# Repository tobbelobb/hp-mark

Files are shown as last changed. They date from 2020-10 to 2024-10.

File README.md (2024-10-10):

# hp-mark hp-mark logo

Measure Hangprinter externally

Current Hangprinters can only measure their own motor positions.
This is useful, but limited.
hp-mark is a separate solution for measuring a Hangprinter's
positions and orientations of anchors and effector.

# High-Level User-Story Dream
 1. Mount a computer-connected camera
 2. Point camera towards build area
 3. BAM! Hangprinter calibrates itself, and gets ready to start printing with fantastic accuracy & reliability

That user experience might be impossible to achieve, but let's get as close as we can.

# Use Cases by Priority
 0. Establish a coordinate system, with z-axis normal to the build plate
 1. The effector as a measurement device: Measure the effector's position and orientation
 2. Calibrate perfect anchor positions
 3. Measure Hangprinter's positional precision and accuracy
 4. Improve accuracy with static compensation matrix
 5. Detect print disasters
 6. Improve precision by dynamically compensating for measured errors

Comment on use case 2: By combining effector position data with the [auto-calibration-simulation-for-hangprinter](https://gitlab.com/tobben/auto-calibration-simulation-for-hangprinter/-/tree/hp_mark_adjusted), we might find perfect anchor positions without having the anchors in-image.

# History, as of Mar 31, 2021
This project was all about getting good pose estimations, for the first 6 months.
hp-mark was developed as a separate measurement system, with no Hangprinter-specific code or hardware.

We have now started manually executing Hangprinter use cases, like homing and anchor calibration.
See <a href="https://www.youtube.com/watch?v=o8oXp44mtUU">demo 0</a>,
<a href="https://www.youtube.com/watch?v=m9qjuZQowCE">demo 1</a>, and
<a href="https://www.youtube.com/watch?v=yRF-zevGHlQ">demo 2</a>, and
<a href="https://youtu.be/As3Y5J2NTGA">demo 3</a>.

Ahead of us now, is automating it more.

# Status
We can estimate poses with one camera, stably and reliably. [Tweet](https://twitter.com/tobbelobb/status/1377256553665990659).

 - [x] Acquire hardware
 - [x] Calibrate camera
 - [x] Acquire training/benchmark images
 - [x] Calculate one 3D point from one marker
 - [x] Calculate _n_ single points from _n_ markers
 - [x] Calculate 6D pose from 6 points (solve perspective-6-point, or P6P problem)
 - [x] Acquire camera 6D pose (this includes defining our world coordinate system)
 - [x] Acquire effector 6D pose
 - [x] Detect all markers on 95% of training images
 - [x] Create a continuous stream of position measurements (video?)
 - [x] Get a statistical idea about size of error at the origin
 - [ ] Respond to RepRapFirmware/Duet request for position measurement

A checked box above means "good enough for now".

Nice-to-haves:

 - [ ] Take image ourselves upon request, don't rely on other programs to take image first
 - [ ] Get a statistical idea about size of precision and accuracy in the whole measurement volume
 - [ ] Integrate a second camera, to reduce error

# Equipment
 - Raspberry Pi 4 (mine is Model B, 2GB RAM)
 - Arducam 8 MP Sony IMX219 camera module
 - Lens: M2504ZH05 Arducam lens
 - 32GB U3 SD card
 - Default recommended Raspberry Pi OS, 32-bit
 - OpenCV 4.4.0
 - EDLib for ellipse detection
 - Probably a separate computer ("desktop" or "laptop" or "main computer") for running hpm. You can run hpm directly on the Raspberry Pi, but it's slow.

# How To Clone/Pull This Repository

 - Clone with `git clone --recursive https://gitlab.com/tobben/hp-mark.git`. The `--recursive` is there to make sure you get the `hpm` submodule.
 - If you already did `git clone` without `--recursive`, do `git submodule init && git submodule update` to get submodule code right.
 - When you pull the hp-mark repo, since the `hpm` submodule might also have changed since last time, do either one of
   ```
   git pull; cd hpm; git pull; cd ..
   ```
   or
   ```
   git pull --recurse-submodules
   ```

# How To Use This Repository

First calibrate your camera.
How to do that is described in [the README.md in camera-calibration directory](./camera-calibration/README.md).

Then compile `hpm`.

# hpm
hpm is the core part of hp-mark.
It is a program that reads data from the camera, and outputs a pose (three rotational values, three translational values).

## hpm Dependencies
This repo will (for now) assume that a number of dependencies are already installed by the user.

#### Main Computer
 - OpenCV 4.2.0 or later
 - g++ version 10 or later
 - build2 version 0.13.0 or later (not required if you're only going to build once)
 - clang++ version 10 or later (not required for build & use)
 - clang-tidy version 10 or later (not required for build & use)
 - clang-format version 10 or later (not required for build & use)
 - compiledb (not required for build & use)
 - shfmt (not required for build & use)
 - python3 (not required for build & use)
 - black (not required for build & use)
 - scipy (not required for build & use)
 - numpy (not required for build & use)

#### Raspberry Pi 4
 - rpicam-still (shading fix required if you don't use standard Raspberry Pi Picam. For why, and how to get the right shading fixes for Arducam lenses see [here](https://www.arducam.com/docs/cameras-for-raspberry-pi/native-raspberry-pi-cameras/lens-shading-calibration/).)

### Why Are Some Dependencies Not Required for hpm Build & Use?
Scripts `tidy.sh`, `make-compilation-database.sh`, `format.sh` etc are there to softly enforce some coding quality and standards.
It you're not going to change the code anyways, then you don't need the scripts nor their dependencies.

### Why Is build2 Not Required Always?
build2 is a fast build system, but it takes a while to get it.
If you only need to build once, you can build without any build system, and use the script `hpm/hpm/slow_build.sh` instead.

It will be a very slow build, but it will take less time than it would have taken
to acquire build2.

## hpm How To Build
First, you need a fairly recent version of OpenCV installed somewhere in your C++ compilers' search path.
You can probably use your system's package manager. On Ubuntu, something like
```
sudo apt install libopencv-dev
```

If you're on another system, see OpenCV's or your operating system's official build/install instructions.

Back in the day, I had to build OpenCV myself.
See <href="./doc/simplest-hpm-compilation-ubuntu-20.04">simplest-hpm-compilation-ubuntu-20.04</a> if you for some reason need to do that.

### For Users Who Only Build Once
```
sudo apt install libopencv-dev
cd hp-mark/hpm/hpm
./slow_build.sh --no-tests
```

Then try running the resulting `hpm` binary:
```
./hpm --help
```

I'm not using it directly most of the time.
Rather, I'm using it via the scripts found in
the hp-mark/use directory

### For An Advanced User Who Wants To Build Repeatedly
Build with build2. See <a href="https://build2.org">build2.org</a> for install instructions.

Before building `hpm` with build2, its recommended to create a build configuration.
No pre-configured build configuration is shipped with this project, and build2's default configuration works poorly with hpm.

```
cd <path-to>/hp-mark/hpm
bdep init --config-create ../my-build-dir @user cc config.cxx=g++-10
```
This creates a build2 config, gives it the location `../my-build-dir`, the name `@user`, and the compiler `g++-10`.
Compile with
```
b
```

### If You're a Developer Making a Pull Request
Create a configuration with some more compiler flags than the user:
```
cd <path-to>/hp-mark/hpm
#in < path - to > / hp - mark / hpm
bdep init --config-create ../my-advanced-config @developer cc config.cxx=g++-10 config.cxx.coptions="-g -Wall -Wextra -Wold-style-cast -Wnon-virtual-dtor -pedantic -Wcast-align -Wunused -Woverloaded-virtual -Wpedantic -Wconversion -Wsign-conversion -Wmisleading-indentation -Wnull-dereference -Wdouble-promotion -Werror -O2 -march=native"
```
You can edit your personal or compiler specific flags later, in `<path-to>/hp-mark/my-advanced-config/build/config.build`.
Some example flags for reference can be seen in `<path-to>/hp-mark/hpm-gcc/build/config.build`.

Compile with
```
b test
```
which will build and test using your default build config.

Symlinks to executables end up in `<path-to>/hp-mark/hpm/hpm/`.
The executables themselves, as well as build artifacts, end up in `../my-build-dir/hpm/hpm/` or `../my-advanced-config/hpm/hpm/`, depending on which build you updated.

Create as many configs as you want.
One that cross compiles for the Raspberry Pi 4 might be particularly useful in the later stages of this project, when build times get noticeable.

You can see all your configs, and which of them is the default with
```
bdep config list
```
bdep is a very flexible and useful command. See its documentation [here](https://build2.org/bdep/doc/bdep-config.xhtml).

I use [some own notes](https://gitlab.com/hangprinter/linc/-/blob/master/README.md) for remembering build2 commands.

## How To Run
Your executable should tell you how it wants to be used.
Ask it like this:
```
<path-to>/hp-mark/hpm/hpm/hpm
```
or, like this:
```
cd <path-to>/hp-mark/hpm/hpm/
./hpm
```

The executable will tell you that it wants some camera parameters (a config file).
Examples of camera parameter configs are given in `hp-mark/hpm/hpm/example-cam-params/`.
They contain the outputs of your camera calibration, as well as `camera-rotation` and
`camera-translation` that are created by `hpm` itself, if it's executed with the `-c/--camera-position-calibration` flag.

To get the correct `camera-rotation` and `camera-translation`:

 1. Place your effector at home position (nozzle in origin, lines tight, effector horizontal).
 2. Mount your camera in it's final position, pointing towards the effector.
 3. Take the image (and maybe download to your main computer, if that's where you execute `hpm`).
 4. Run `$ ./hpm <your-half-finished-camera-parameters-file> <marker-parameters> <image-file> --camera-calibration`

### But Wait, We Don't Have The Correct Marker Parameters Yet!
True. Marker parameters is another config file, that describes your markers.
Examples of such configs are found in `hp-mark/hpm/hpm/example-marker-params/`.
They contain:

 * Maker positions on the effector
 * Marker type on the effector
 * Marker size on the effector
 * Optionally: marker positions on the bed
 * Optionally: marker type on the bed
 * Optionally: marker size on the bed

Your marker type is most probably disk, but hpm also supports sphere.
Your marker diameter is 90 mm if you follow my standard example. Bigger is generally better.
Your marker positions are a bit more complicated.
We want their xyz positions relative to the tip of the nozzle, in a coordinate system that looks like this:

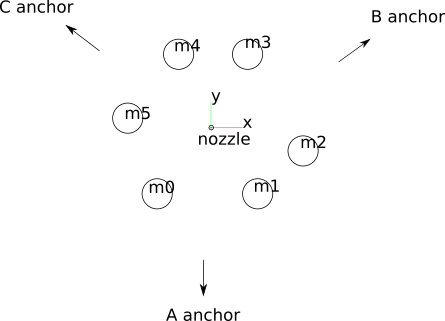
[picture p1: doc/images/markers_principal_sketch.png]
markers principal sketch


It's very hard to take these xyz measurements directly.

You have two options for how to get these xyz measurements.

#### Option 1: Try Markers Positions Detector

Getting the xyz measurements of the markers can be done with computer vision. Dzardajs (aka Github user matusbalazi) has made [Markers Positions Detector](https://github.com/matusbalazi/markers_positions_detector) to help you do that. At the time of writing (April 8, 2022) Markers Positions Detector is still quite new, but I recommend that you try this out first if you already have a well-calibrated camera.

#### Option 2: The find-marker-positions.py Script

This is the old way, like a precursor to Markers Positions Detector.

If you want to use find-marker-positions.py, there will be 21 manual measurements.
They are all either between the center of a marker to the tip of the nozzle,
or between two centers of markers.
Referring to the image, Make the following measurements in the following order:

 * nozzle-m0, nozzle-m1, nozzle-m2, nozzle-m3, nozzle-m4, nozzle-m5
 * m0-m1, m0-m2, m0-m3, m0-m4, m0-m5,
 * m1-m2, m1-m3, m1-m4, m1-m5,
 * m2-m3, m2-m4, m2-m5,
 * m3-m4, m3-m5,
 * m4-m5.

Armed with these 21 values (in units of millimeters), do
```
cd hp-mark/find-marker-positions
./find-marker-positions.py --measurements <all measurements here in correct order, separated by spaces>
```
Alternatively, you can type in your 21 values into the `find-marker-positions.py` script directly. It's near the bottom of the file.
I you do type in directly into the file, you can execute the script with no arguments:
```
./find-marker-positions.py
```

If you get a cost below ca 3, you're probably good.
Copy/paste the final values you get into your marker-params config file.

Congrats! You should now be able to measure the position of your effector with hp-mark.
Take a few test images and see if it works.

#### Usage Via SSH

After a while, it gets cumbersome to always have to download the image from the Raspberry Pi to the main computer manually,
so I've written some scripts to speed that up.

Look into:

```
<path-to>/hp-mark/use/use_ssh_continuous.sh
```

Open it, change `CAMPARAMS` and `MARKERPARAMS` variables so they point to your two new config files.
It accepts the same flags as `hpm` does, so take it for a ride for example like
```
./use_ssh_continuous.sh --show result
```
... and press Enter to get another image, or ctrl-C to exit.

### How to get external camera parameters?
After the correct camera calibration you obtained internal camera parameters stored in the `myCamParams.xml` file.
Then you found markers positions on the effector which are also stored in the XML file.
Last thing we have to do to use hp-mark is to find out external camera parameters (rotation and translation of camera).

I made simple script which will make it easier and faster for you.
It runs hpm, analyzes input image, generates XML file with external camera parameters and merges
internal and external cam params into one XML file.

All you need is:
 * XML file with internal camera parameters
 * XML file with markers parameters
 * image of your effector with markers placed on it

Now install colorama package by typing to command line:

```
sudo apt update
sudo pip install colorama
```

Then run:

```
python3 <path-to>/hp-mark/hpm/hpm/get_cam_params.py
```

There is a bunch of arguments you can add to speed up later process:
 1. `-f1` or `--xmlC` means path to the internal cam params XML file
 2. `-f2` or `--xmlM` means path to the markers params XML file
 3. `-f3` or `--image` means path to the input image which will be analyzed

So the command to run this program can look like this:

```
python3 <path-to>/hp-mark/hpm/hpm/get_cam_params.py --xmlC <path-to>/myCamParams.xml --xmlM <path-to>/myMarkersParams.xml --image <path-to>/image.jpg

```

After that `myCamParams.xml` should be generated in the same folder as `get_cam_params.py` is.
Last thing you have to change is `CAMPARAMS` variable in `use_ssh_continuous.sh` file so it points to your new config file.

Another important script, which also tries to move the Hangprinter's effector around between images is called
`get_auto_calibration_data_automatically.sh`.
I won't get into detail about that here. Some detail is offered in the hangprinter.org docs.

# Remaining Development Challenges
 - The cameras' positions are estimated from images of known patterns. The results' accuracy are limited by errors in the markers and errors in the camera calibration values
 - We must calibrate the camera lens to compensate for optical distortion. This is time consuming and hard. The lo-distortion lens from Arducam helps a bit, but not all
   the way.

# Opportunities & Smaller Use Cases
 - There's an interesting PnP solver on its way into OpenCV that seems very good: [Added SQPnP algorithm to SolvePnP (2020)](https://github.com/opencv/opencv/pull/18371)
 - Distances between nozzle and markers may be measured by placing the nozzle on a marker, and letting hp-mark measure relative distances.
 - We can add features in the future that control the image processor (to compensate distortion predictably, or for other tasks). An image processor can do [lots of things](https://webpages.uncc.edu/jfan/isp.pdf). The Raspberry pi 4 and libcamera gives us the perfect tools for the job:
   * [raspberrypi.org page about libcamera](https://www.raspberrypi.org/documentation/linux/software/libcamera/)
   * [libcamera's own home page](http://www.libcamera.org/)
   * [Blog post announcing libcamera](https://www.raspberrypi.org/blog/an-open-source-camera-stack-for-raspberry-pi-using-libcamera/)

# Keywords
 camera localization, pose estimation, motion tracking, optical sensors, vision-based registration, marker-based tracking techniques, fiducial marker localization

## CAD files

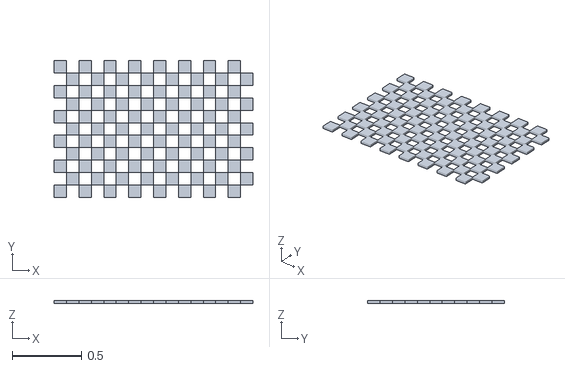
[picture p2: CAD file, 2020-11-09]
camera-calibration/calibrate_openscad_camera/chessmesh.stl
1.44 x 0.99 x 0.02

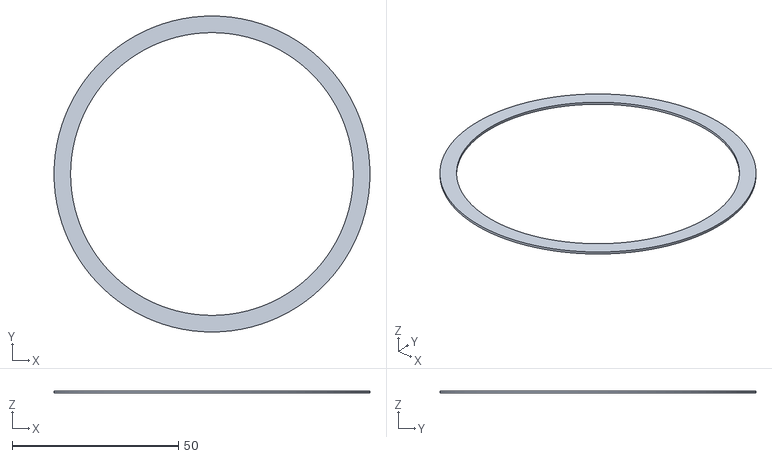
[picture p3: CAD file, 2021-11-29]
markers/flat_markers/contrast_edge.stl
95.0 x 95.0 x 0.7

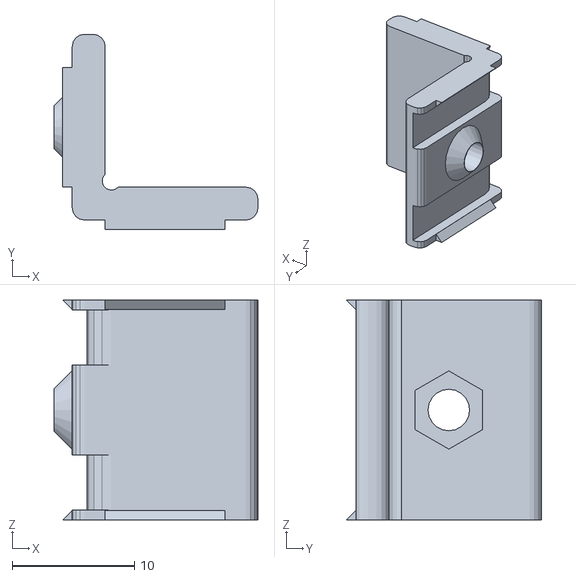
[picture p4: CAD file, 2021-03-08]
markers/marker_slider.stl
16.7 x 16.0 x 18.0

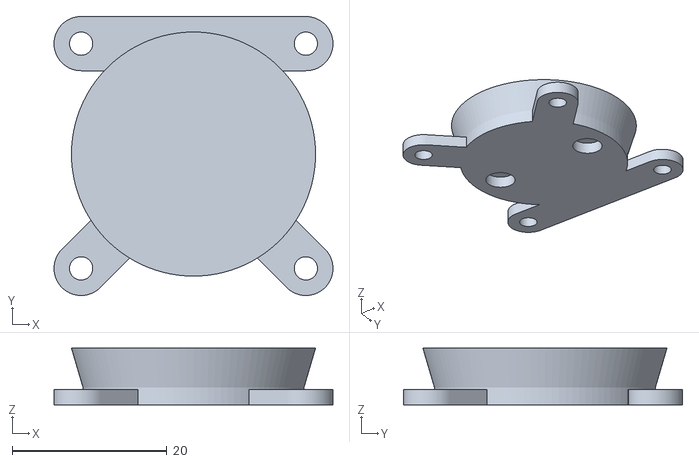
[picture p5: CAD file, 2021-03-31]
picam-mount/snrreskive2_arducam.stl
36.0 x 36.0 x 7.30

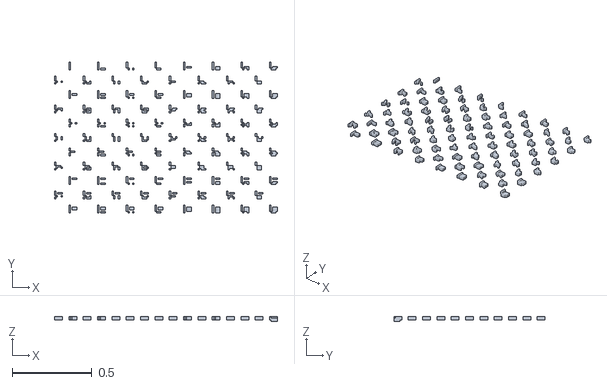
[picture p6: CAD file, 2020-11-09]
camera-calibration/calibrate_openscad_camera/charucointernal.stl
1.40 x 0.95 x 0.03

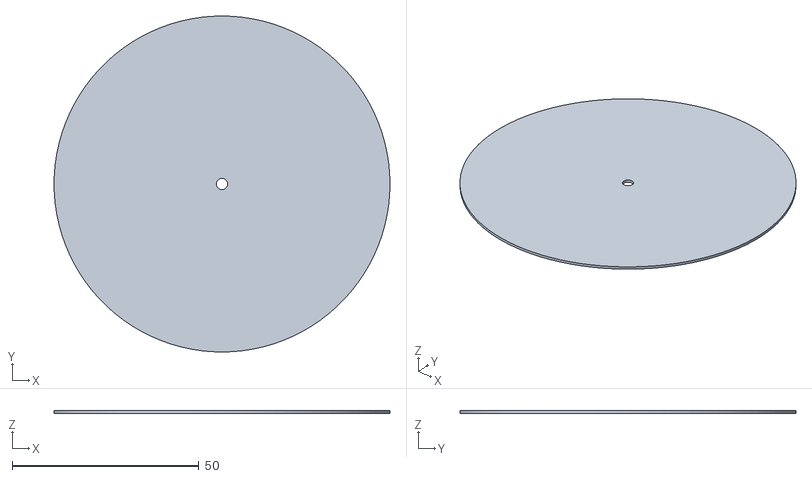
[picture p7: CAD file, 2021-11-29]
markers/flat_markers/retroreflective_plate.stl
90.0 x 90.0 x 0.7

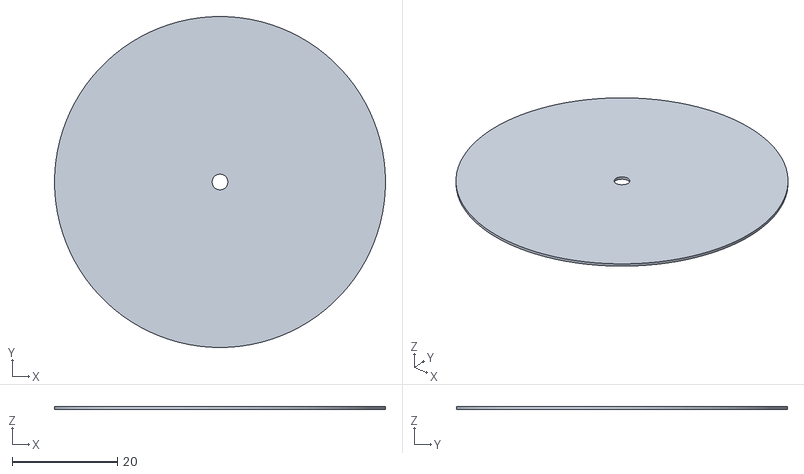
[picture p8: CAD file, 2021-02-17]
markers/spherical_markers/bg_plate.stl
63.0 x 63.0 x 0.5

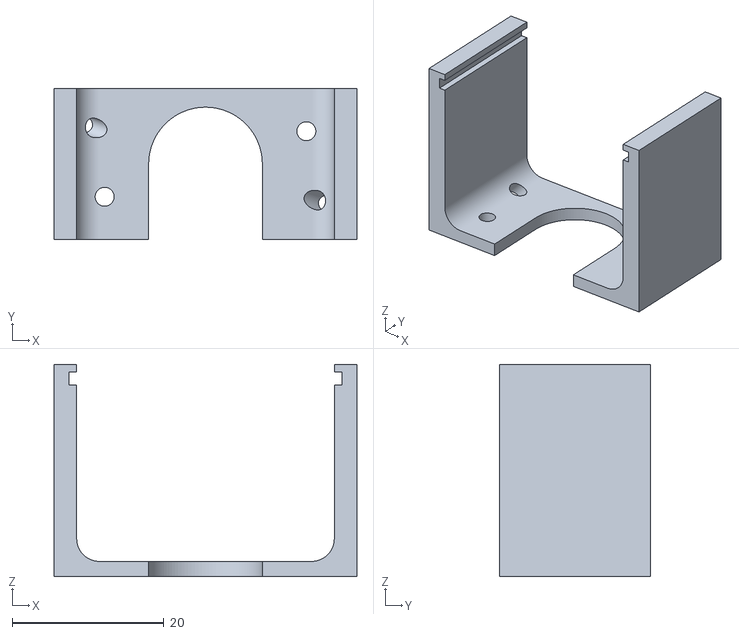
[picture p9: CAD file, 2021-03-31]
picam-mount/led_holder_arducam.stl
40.0 x 20.0 x 28.0

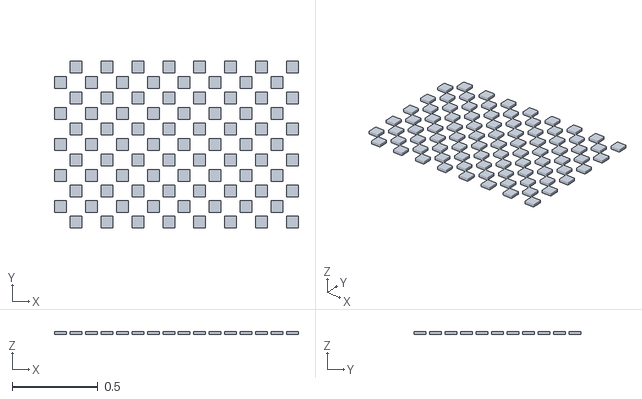
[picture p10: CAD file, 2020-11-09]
camera-calibration/calibrate_openscad_camera/charucomesh.stl
1.42 x 0.97 x 0.02

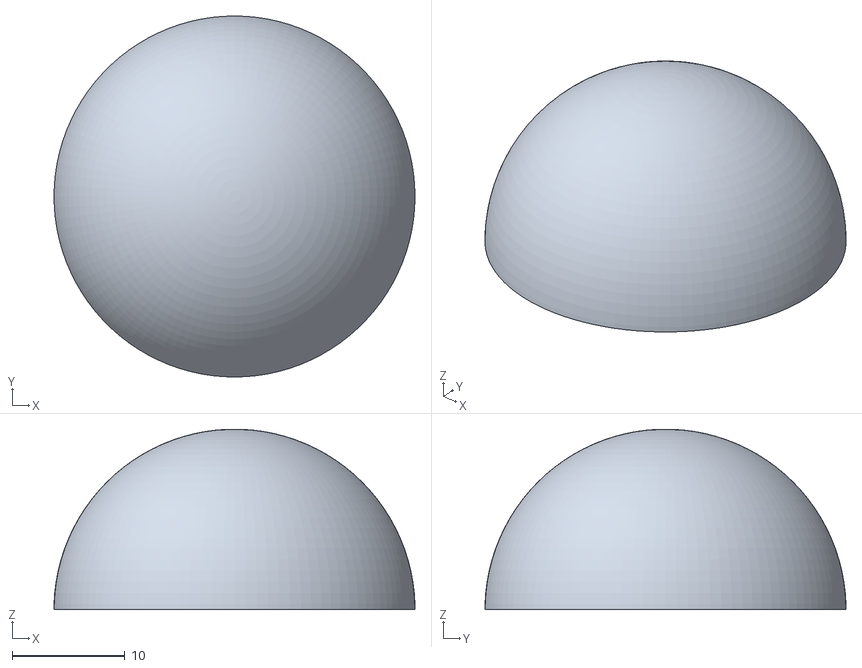
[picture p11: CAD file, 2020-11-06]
markers/spherical_markers/top_cap.stl
32.0 x 32.0 x 16.0

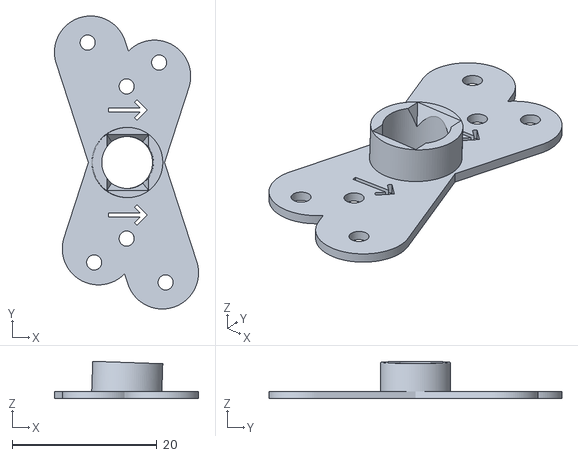
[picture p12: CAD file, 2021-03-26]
picam-mount/lens_hood.stl
19.9 x 40.4 x 5.17

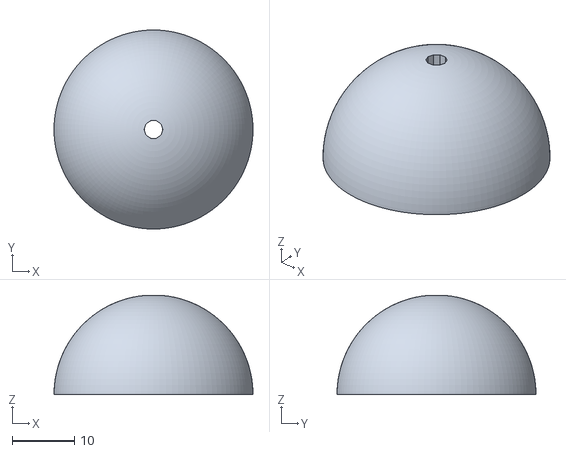
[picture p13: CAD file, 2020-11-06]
markers/spherical_markers/bottom_cap.stl
32.0 x 32.0 x 15.9

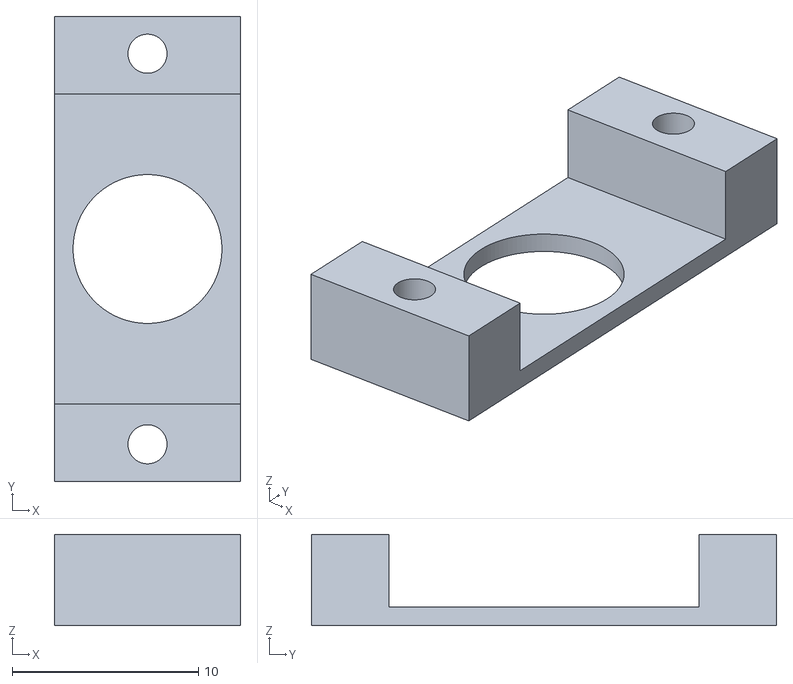
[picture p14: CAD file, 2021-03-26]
picam-mount/lens_hood_legs.stl
10.0 x 25.0 x 4.90

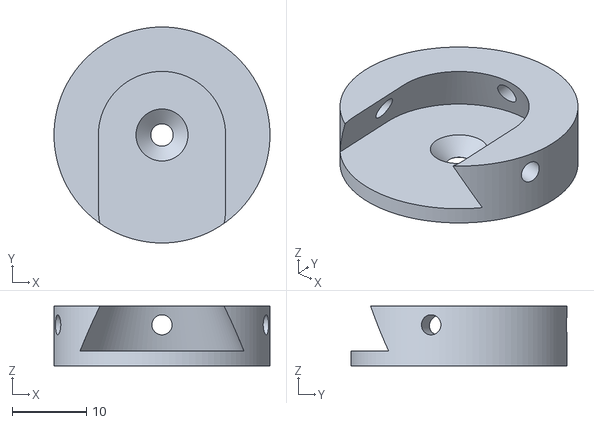
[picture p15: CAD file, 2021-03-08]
picam-mount/base.stl
29.0 x 29.0 x 8.00

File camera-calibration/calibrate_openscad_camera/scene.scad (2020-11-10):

// For some reason, we've lost perfect squareness by ~.1%
// It might be the pdf that is off, or it might be the program
// pdf2svg that has bad truncation errors internally,
// or it might be Blender that has the truncation errors.
// Blender was used to convert the intermediate svg image into
// chessmesh.stl, charucomesh.stl, and charucointernal.stl
measured_x_length = 1440.0297403;
measured_y_length = 989.8103476;

// With these lengths, each chess square side is 90 mm wide
// And each marker is 70 mm wide
wanted_x_length = 1440;
wanted_y_length = 990;

translate([-wanted_x_length/2, wanted_y_length/2, 0]) {
  scale([wanted_x_length/measured_x_length, wanted_y_length/measured_y_length,1]) {
    color("black")
      scale([1000, 1000, 0.005])
      import("./chessmesh.stl");
    color("black")
      scale([1000,1000,0.005])
      import("./charucomesh.stl");
    color("white")
      translate([0,0,-0.0005])
      scale([1000,1000,0.25])
      import("./charucointernal.stl");
  }
}
//$t=0.7;

// Ok, but not fantastic values
//$vpr = [45,0,360*$t];
//$vpt = [130*sin(360*$t),-130*cos(360*$t),0];
//$vpd = 2500+1000*abs(sin(360*2*$t));

// For animating a bunch of frames, you can use this
vprs = [[ 49.90, 0.00, 359.60 ],
        [ 52.70, 0.00, 29.00 ],
        [ 53.40, 0.00, 60.50 ],
        [ 46.40, 0.00, 90.60 ],
        [ 47.80, 0.00, 120.70 ],
        [ 42.90, 0.00, 154.30 ],
        [ 34.50, 0.00, 180.20 ],
        [ 50.60, 0.00, 196.30 ],
        [ 52.00, 0.00, 221.50 ],
        [ 48.50, 0.00, 261.40 ],
        [ 49.20, 0.00, 279.60 ],
        [ 51.30, 0.00, 323.70 ]];
vpts = [[ -2.39, -66.23, 37.04 ],
        [ 37.14, -122.39, -54.19 ],
        [ 136.35, 12.34, -81.12 ],
        [ 107.45, 12.39, -49.25 ],
        [ 91.81, 65.31, -63.52 ],
        [ 80.53, 52.77, -48.47 ],
        [ -7.27, 54.79, -48.38 ],
        [ 50.34, 79.79, -78.75 ],
        [ -94.89, -6.90, -120.59 ],
        [ -75.61, -43.08, -92.93 ],
        [ -73.70, -38.31, -89.82 ],
        [ -90.66, -35.63, -99.43 ]];
vpds = [2264.24, 2296, 2557, 2547.78, 2886, 2800, 2215, 2215, 2673, 2673, 2673, 2592];

// Writing a bash script with OpenScad echo function...
//for (i=[0:len(vprs)-1]) {
//  echo(vpts[i], vprs[i], vpds[i]);
//}

//index = round($t*len(vprs));
//$vpr = vprs[index];
//$vpt = vpts[index];
//$vpd = vpds[index];

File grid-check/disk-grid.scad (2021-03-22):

// Use command line to create renders.
// For example

// openscad --camera 0,0,0,0,0,0,2000 --imgsize 15360,8058 --colorscheme Nature --projection perspective -o grid-blue-2000.png sphere-grid.scad


$fn=2000;

squareWidth = 100;
gridWidthx = 7;
gridWidthy = 4;
//$vpt=[0,0,0];
//$vpr=[0,0,0];
//$vpd=2000;

for (nx = [-gridWidthx:gridWidthx])
  for (ny = [-gridWidthy:gridWidthy])
    translate([nx*squareWidth, ny*squareWidth, 0])
      color([1,1,1])
        cylinder(d=70, h=0.01);

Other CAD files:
picam-mount/vippeplate.stl
picam-mount/snurreskive.stl
picam-mount/snurreskive2.stl
markers/spherical_markers/screw.stl
grid-check/sphere-grid.scad
grid-check/tilted-disk-grid.scad
camera-calibration/calibrate_openscad_camera/test.scad
markers/marker.scad
markers/revolve2.scad
picam-mount/picam_mount.scad

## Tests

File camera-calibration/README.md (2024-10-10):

# How To Calibrate PiCam v2 for hp-mark

We're going to use a [charuco board](https://docs.opencv.org/4.4.0/da/d13/tutorial_aruco_calibration.html)
as our pattern.

We're also going to use [a non-linear optimization method](https://elib.dlr.de/71888/1/strobl_2011iccv.pdf)
to compensate for the paper with the charuco board on being every so slightly non-flat.

## Preparations

Read this whole document first.
You might want to do things in a different order than described here,
so read the whole document first to avoid time consuming surprises later.
You can always come back here and follow step-by-step later.

Print the charuco board pdf as large as you can.
Tape/glue your charuco board down as flat and straight as possible.

Compile and take the camera calibration program for a test run:
(Warning: this takes a few minutes to run on the Raspberry pi 4.)
```
cd <path-to>/hp-mark/camera-calibration
./doit.sh
```

If everything went smooth, an output file `myCamParams.xml` should have been created.
It contains nonsense, but we hopefully confirmed that the compiler and the program itself are working.

Next remove it and the test images.
(Take a look at them first, they should be decent examples.)

```
rm myCamParams.xml pics/camera*
```

## How To Take Calibration Images

The duet3 official Raspberry Pi OS image comes with the camera disabled by default.
To enable it do
```
sudo raspi-config
[Interface Options] -> [Camera] -> [Enable] -> [Reboot yes]
```

Take your own pics inside the pics directory.
```
cd pics
./takeCalibrationStills.sh
```

Press Enter to take a picture, press X followed by enter before the last image.

Regardless if your first pics are good or bad, put their names in the `pics_list.xml`, and
execute `doit.sh` like before.
You will probably get an error the first time, because all the corners could not be identified in
some, or all of your image(s).

Look into the script `takeCalibrationStills.sh` and adjust each of the flags to `rpicam-still`
until you get nice image quality.

Take note of the `-fs/--framestart` flag.
Increment the framestart if you want to avoid overwriting previously taken images.

We want to not have over-exposure, as it would affect calibration negatively.
Reduce the `--shutter` time until the white squares look light grey on your image.

Also, adjust the focus of your Picam v2.
Optimize for the distance range of the final use case, not for the calibration itself.
If you later change the focus, you will need to re-calibrate the camera.

## How To Take Good Calibration Images

Read [Dr. Strobl's invaluable calibration hints](https://www.dlr.de/rm/en/desktopdefault.aspx/tabid-3925/6084_read-9196/).
Here's a procedure that tries to take the advice into account as much as we can in our use case:

  * Fasten your Picam to a camera tripod or similar, at 25-27 cm height
  * Move the camera around the pattern and take images
  * Fill as large portion of the image with squares as you can
  * All aruco markers must be in every image
  * Don't touch or move the pattern between images
  * Take half of the images with the camera mounted upside down (otherwise we risk getting better calibration in the upper half of the image, where focus is sharper)

Here's an image of my "imaging lab" during calibration image grab.

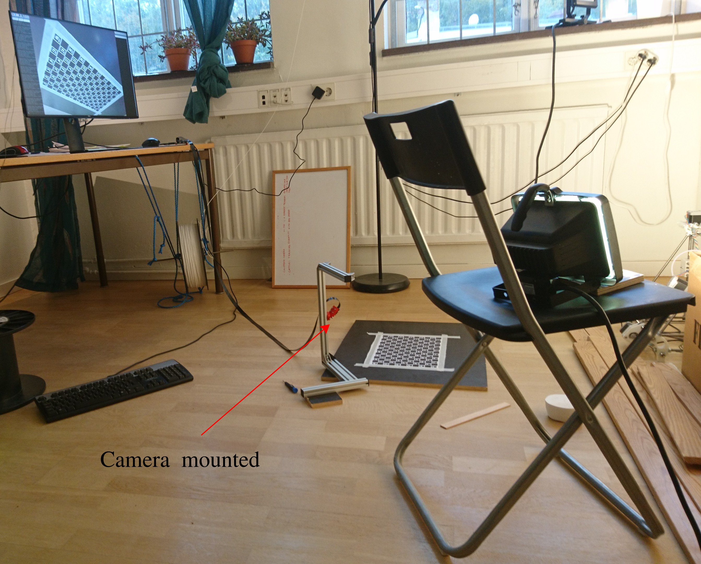
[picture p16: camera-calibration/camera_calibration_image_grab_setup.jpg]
camera calibration image grab setup


If you have a large flatish screen, you may just display the pattern on that screen, instead of printing it on paper:

camera calibration pattern shown on screen.

## How To Use the Calibration Images Well

Run `./doit.sh` to double check that all corners of all images in `pics_list.xml` are detected.
You might get better detection my incrementing/decrementing `adaptiveThreshWinSizeStep` inside `detector_params.yml` by 1 or 2.
There's [a whole tutorial](https://docs.opencv.org/4.4.0/d5/dae/tutorial_aruco_detection.html) about Aruco detection in the OpenCV documentation.

Once you have 10-20 good images with full corner detection in your `pics_list.xml`, it's time to do some final tuning.

Measure the square side length of your charuco board as accuratly as you can.
If your paper is even slightly wrinkled, remember that each square will appear shortened by that if you measure across several squares at once.
We don't want to include the losses from paper wrinkling in our measurement, we want the real width of a stretched square.
Also, squares will have different widths on different portions of your paper (unless your printer is really high-end),
so measure several times on different parts of the paper, and use the average of your measured values.

In a similar fashion, measure the side lengths of the aruco markers.
Getting the aruco size really accurate is less important than getting the square size right.
Focus your effort on the square size.

Open `doit.sh` and feed in your measured `--square_side_length` and `--marker_side_length`.
It doesn't matter which units you use.

The last value we need is the `--grid_width`:

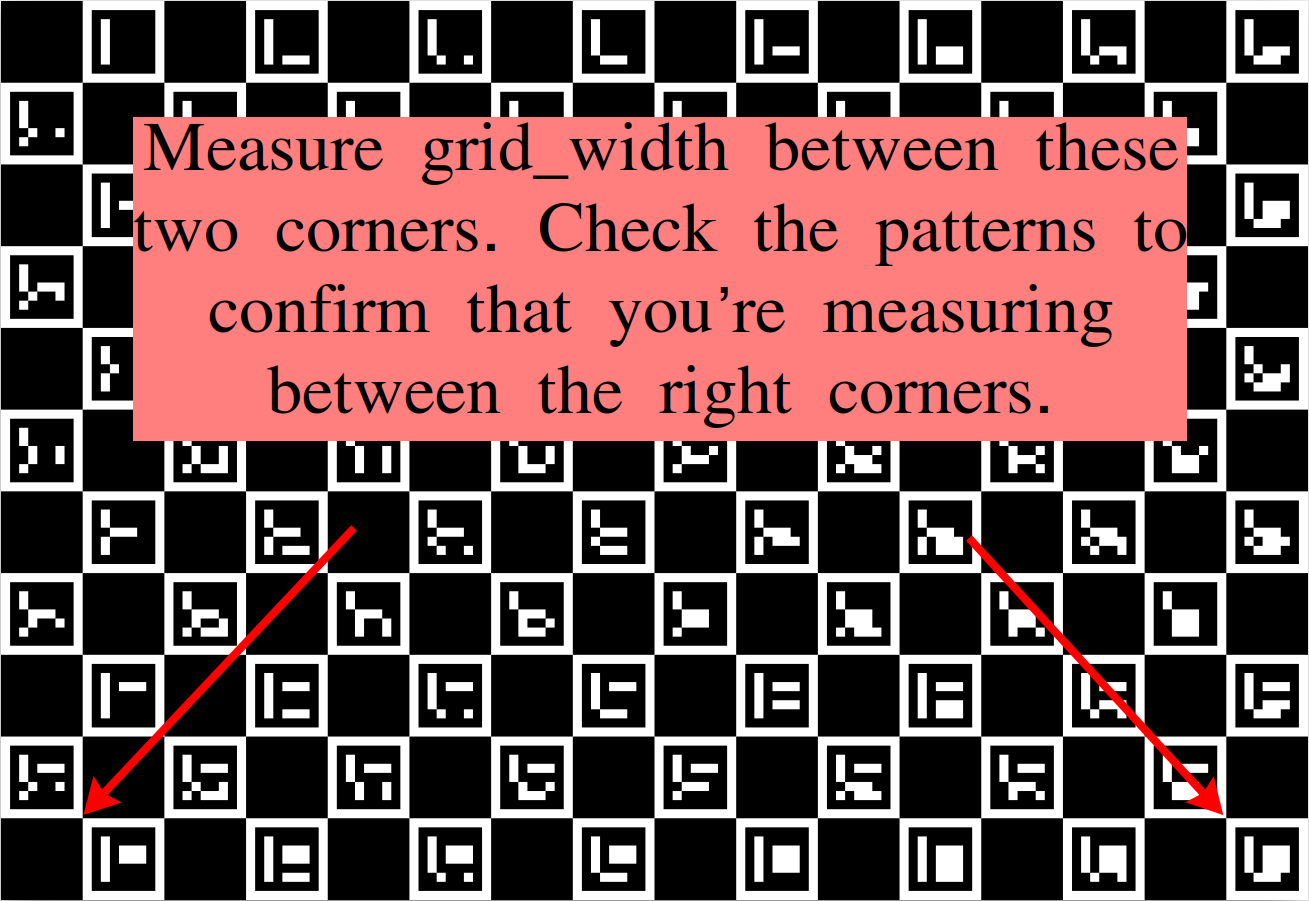
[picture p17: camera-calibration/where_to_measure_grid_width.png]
Where to measure the grid_width


In the grid width measurement, we do want the effects of paper wrinkling to be included in the measurement.
So you want a slightly lower value than `14 x square_side_length`.

The algorithm will try to understand how wrinkled your paper is, as described in [this paper](https://elib.dlr.de/71888/1/strobl_2011iccv.pdf).

Once the right `grid_width` is inserted into `doit.sh` it's time for the final calibration.
One last time, run:
```
./doit.sh
```
If everything went smooth, you'll get a small reprojection error.
An output file `myCamParams.xml` should have been created.
It should now contain the intrinsic parameters for your PiCam v2.

### What is a 'small' reprojection error?
I don't really know how small this value needs to be, but I would consider anything below 0.6 a great success.
I'm currently using a setup with 0.48 error myself.

If you've already spent a good amount of time, and are unable to get below a given reprojection error limit, I generally advice settling with the best you have so far,
and revisit camera calibration later, if it turns out to be crucial for your application.

In for example a high-stakes project that turns out to rely heavily on hp-mark, it might be worth it to buy some more high-end cameras, that are either pre-calibrated,
or much easier to calibrate.

As a reference, I generated synthetic calibration images straight out of OpenScad.
These images should be close to perfect, since there is no real camera involved.
Still, when I fed these images into `calibrate_camera_charucoRO`, I still couldn't get the reprojection error below 0.2.

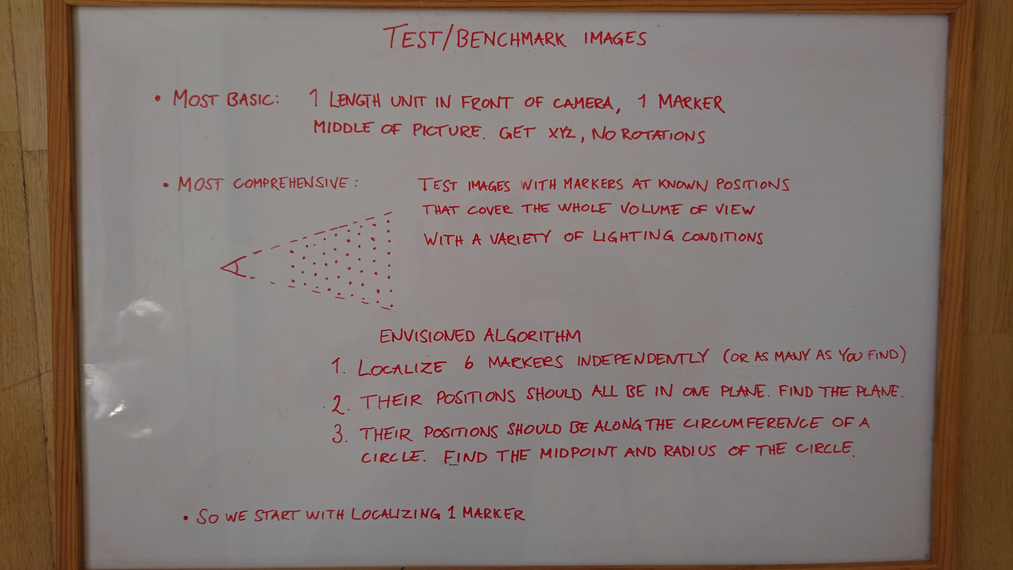
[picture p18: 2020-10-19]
doc/whiteboards/2_what_benchmark_images_do_we_want_start_with_localizing_one_marker.JPG

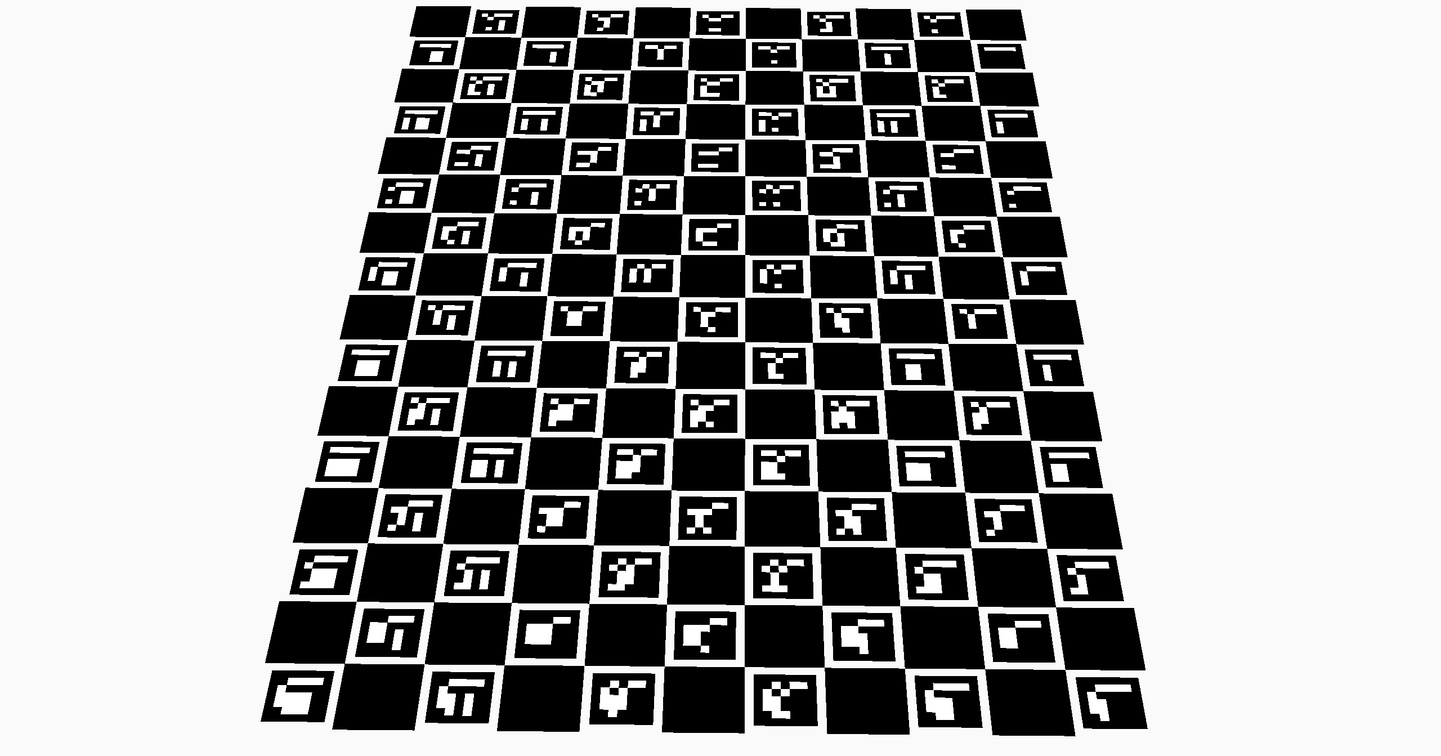
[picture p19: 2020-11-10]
camera-calibration/calibrate_openscad_camera/frame00003.png

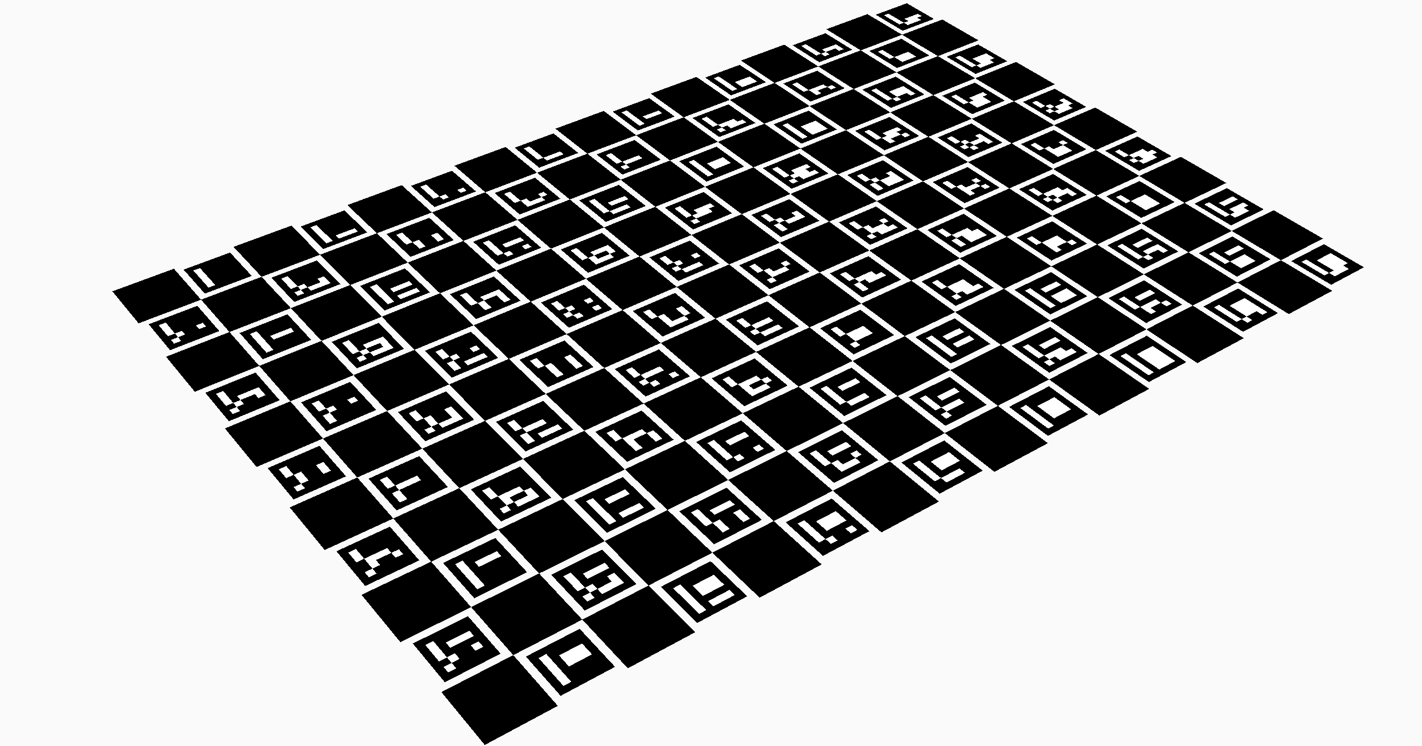
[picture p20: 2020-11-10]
camera-calibration/calibrate_openscad_camera/frame00011.png

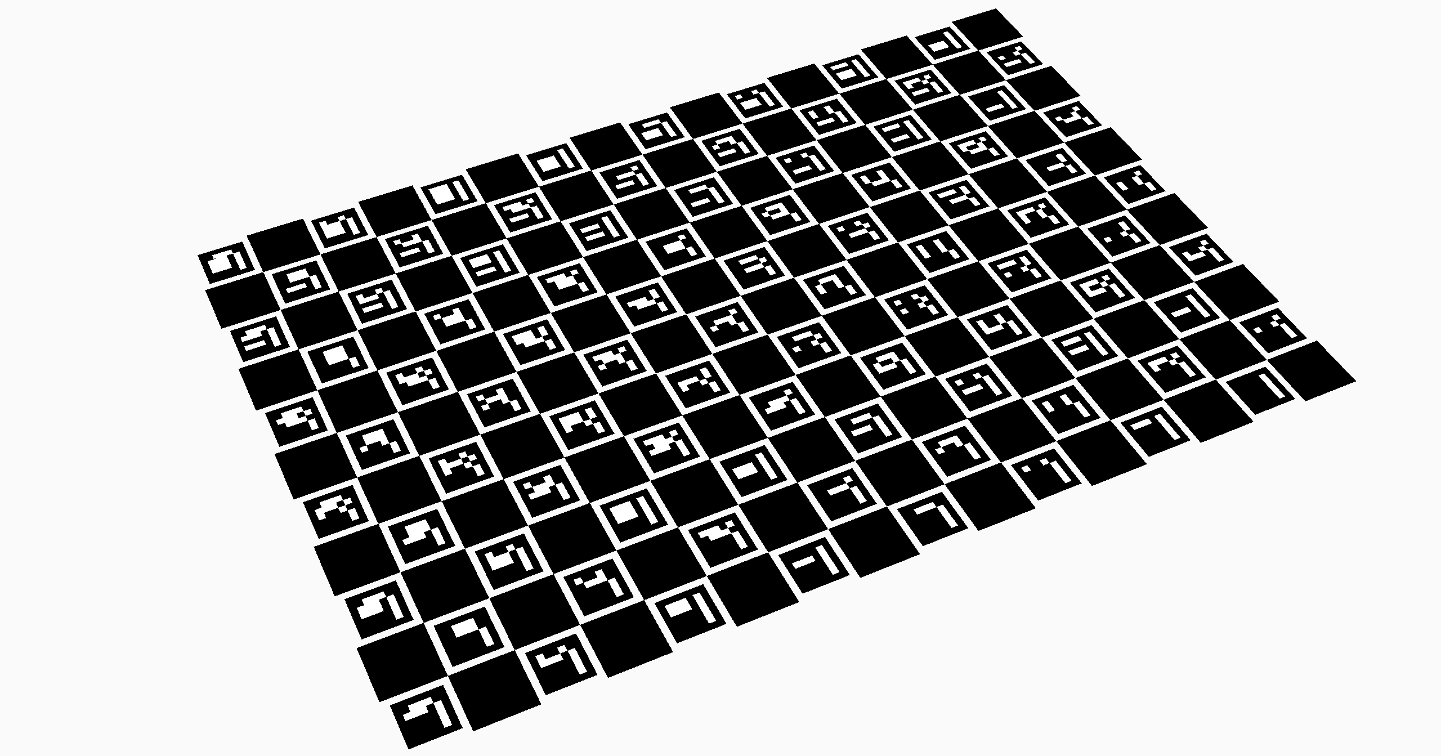
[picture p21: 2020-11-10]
camera-calibration/calibrate_openscad_camera/frame00005.png

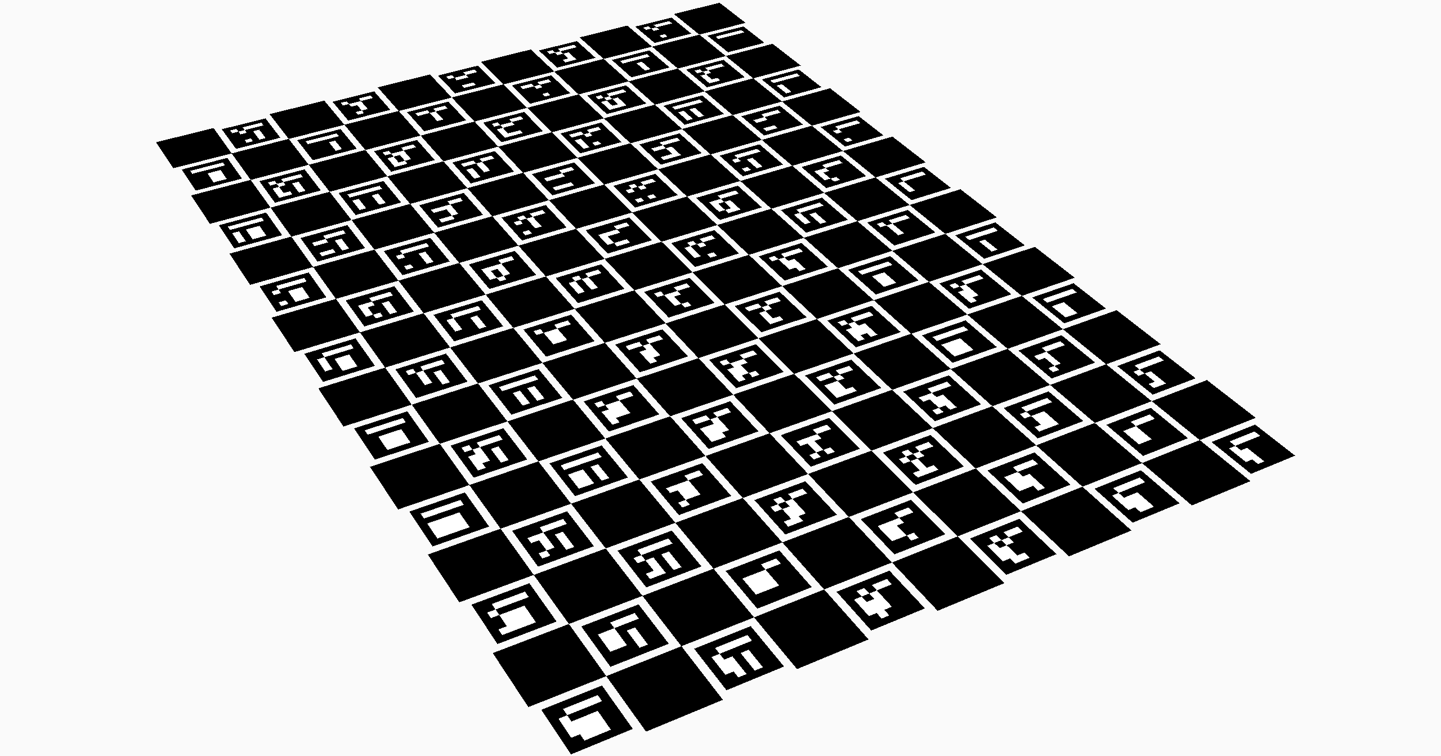
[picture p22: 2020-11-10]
camera-calibration/calibrate_openscad_camera/frame00002.png

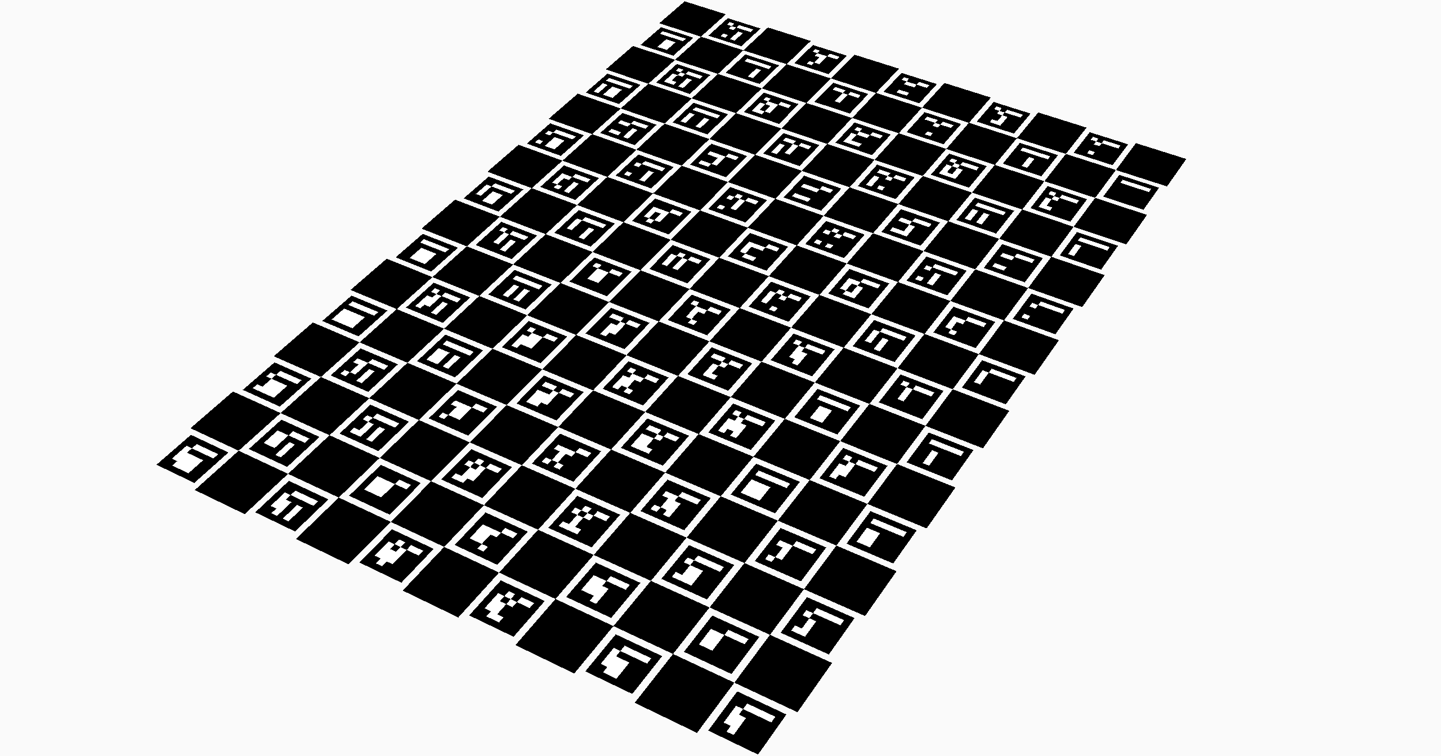
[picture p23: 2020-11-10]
camera-calibration/calibrate_openscad_camera/frame00004.png

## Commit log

2020-10-04 Adds first version of spherical markers
    [bottom_cap.stl, revolve2.scad, screw.stl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]
2020-10-05 Changes wall size to print rounder. Also a bit smaller
    [bottom_cap.stl, screw.stl, sphere.scad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]
2020-10-10 Adds notes about how to generate camera calibratino charuco pdfs
2020-10-12 Some progress on camera calibration
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2020-10-13 Manages to get some calibration values out
2020-10-13 Adds code and instructions for calibrating camera
2020-10-15 Changes charuco board slightly
2020-10-15 Changes calibrateCamera to calibrateCameraRO
    See
    https://github.com/opencv/opencv/pull/12772
    and
    https://elib.dlr.de/71888/1/strobl_2011iccv.pdf
    for why this is a good idea.
    It changes how we should take our calibration images though.
    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
2020-10-17 Updates calibration stills command
2020-10-17 Changes args list of calibrate_camera_charuco2
2020-10-17 Changes camera calibration example
2020-10-17 Makes a better camera calibration manual
2020-10-20 Reads in calibration data
2020-11-06 Adds slider piece to mount marker on mover
    Also fixes a bug where threads inside marker sphere were slightly incorrect in a mysterious way.
    Also increases diameter of marker to 32 mm.
    [bottom_cap.stl, marker_slider.stl, screw.stl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]
2020-11-06 Renames file
    [marker.scad]
2020-11-09 Starting structured generation of synthetic images
    Including calibration of synthetic camera (OpenScad)
    [charucointernal.stl, charucomesh.stl, chessmesh.stl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]
2020-11-10 Gets calibration values of the Openscad renderer
    It's a bit of a mystery why reciprocal error does not go to zero.
    The main suspect is truncation effects due to lack of anti-aliasing.
    See this tweet for details on why:
    https://twitter.com/tobbelobb/status/1326198895869882369
    [scene.scad]
2020-11-11 Calibrates the OpenScad camera properly
    [test.scad]
2020-11-27 Adds a lapping helper tool
    See https://twitter.com/tobbelobb/status/1332308653601337346
    for how to use it
    [lapping_helper_tool.stl, marker.scad]
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2021-02-12 Adds a background plate to marker
    [bg_plate.stl, marker.scad]
2021-02-12 Changes marker background plate to lotus style :blossom:
    [bg_plate.stl, marker.scad]
2021-02-17 Makes marker background plate circular and bigger
    [bg_plate.stl, marker.scad]
2021-02-18 Improves find-marker-positions.py
    Measurements between markers are inherently better,
    and also more important than measurements between
    nozzle and markers.
    The optimization is therefore now two-step.
    First, the markers' positions relative to marker 0 are found.
    Then, the nozzle's position relative to marker 0 is found.
    During the second step, only the nozzle position is variable,
    the markers' positions relative to each other is fixed from the
    first step on.
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2021-02-19 Waits for ssh instead of killing it upon C-c
    Also opts in to lots of VERBOSE output.
    Default use case is that we want to create an Octave matrix,
    or a numpy array or something from the output, so we only
    want hpm's output there usually.
2021-02-25 Adds the picam related prints to the repo
    [base.stl, lens_hood.stl, lens_hood_legs.stl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]
2021-02-25 Opens up picam lens hood a little bit
    [picam_mount.scad]
2021-02-26 Reduces load on image sensor for more stable temperature
2021-03-02 Makes screw smaller, and removes lapping tool
    The screw needed to be smaller to make it easier to screw in.
    The lapping helper tool is not needed anymore because
    we don't do lapping anymore.
    We don't do the lapping because it was time consuming,
    and did not improve precision noticably.
    More detailed story:
    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
    [lapping_helper_tool.stl, marker.scad, screw.stl]
2021-03-08 Makes marker sliders easier to use
    [marker.scad]
2021-03-08 Experiments with other types of markers
    [marker.scad]
2021-03-08 Minor improvements to picam mount
    [base.stl, lens_hood.stl, picam_mount.scad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]
2021-03-08 Updates marker slider stl
    [marker_slider.stl]
2021-03-22 Gives grid-check files to disk-check
    [disk-grid.scad, sphere-grid.scad]
2021-03-22 Adds tilted disk grid scad
    [tilted-disk-grid.scad]
2021-03-24 Makes new lens hood w mount for LED rings
    [lens_hood.stl, lens_hood_legs.stl, picam_mount.scad]
2021-03-26 Fixes lens hood light bleed from LEDs
    [lens_hood.stl, lens_hood_legs.stl, picam_mount.scad]
2021-03-26 Removes lens hood flanges
    [lens_hood.stl, picam_mount.scad]
2021-03-31 Small adaptions to change of camera
    Now uses Arducam 8 MP Sony IMX219 camera module,
    with a M2504ZH05 Arducam lens.
    [led_holder_arducam.stl, picam_mount.scad, snrreskive2_arducam.stl]
2021-04-06 Makes use_ssh_continous.sh collect M114 S2
    Also formats output so it can be copy/pasted right
    into the auto calibration code
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2021-04-13 Adds some torque mode commands for later calibration use
    calibration_gcodes.sh
    They try to take the effector to 17 different spots where calibration data
    may be collected.
    Will be merged into use_ssh_continous.sh later.
2021-04-14 Adds flat marker CADs
    [bg_plate.stl, bottom_cap.stl, marker.scad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]
2021-04-15 Gives marker disks a background
    [marker.scad]
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2021-04-15 Adds stl for disk background
    [bg_background.stl]
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2021-04-20 Adds get_auto_calibration_data_automatically.sh
    The script will jog the hangprinter around and collect
    all the needed data for the anchor calibration
2021-04-26 Send G96 from auto cal script
    In case the user forgot do to it.
    It's nice to not neccesarily having to teach the users about G96.
2021-08-23 WIP: Adjusts calibration script to work with HP4.2
2021-09-02 Gives flat marker a contrast edge built in
    [bg_background.stl, marker.scad, retroreflective_plate.stl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]
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2021-11-29 Makes marker two-piece again
    We do this because the retroreflective tape is much easier to cut from
    the back side.
    [contrast_edge.stl, marker.scad, retroreflective_plate.stl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]
2021-12-10 Makes auto calibration script faster
    Changes:
    - how it moves the effector around
    - how it finds a stable motor position
2021-12-11 Waits for user to push enter between each auto calibration measurement
2022-02-04 Updated advice on camera reprojection error
2026-02-08 Fix Charuco board usage for OpenCV 4.11
